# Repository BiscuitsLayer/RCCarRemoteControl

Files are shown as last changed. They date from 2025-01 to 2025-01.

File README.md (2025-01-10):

# План

## Все компоненты

1. Управлять с пульта (когда подаём команды с пульта, то машина сначала останавливается - то есть сбрасывается контроль с ПК)

2. Связь с камерой через удлинитель USB (с питанием) - если можно связь через провода, то лучше всегда её делать

## Настройка машинки

У тачки receiver RX-G3, есть 3 канала, у каждого канала есть по 3 пина

* Самый левый - сигнал (соединяется с белым проводом на машине при управлении только с пульта)
* Средний - питание +5V (соединяется с красным проводом на машине при управлении только с пульта)
* Самый правый - ground (соединяется с красным проводом на машине при управлении только с пульта)

Что-то типа такого ([источник](https://medium.com/@werneckpaiva/how-to-read-rc-receiver-signal-with-arduino-54e0447f6c3f)), только не 9 каналов, а 3, и питание и землю подаём для каждого отдельно

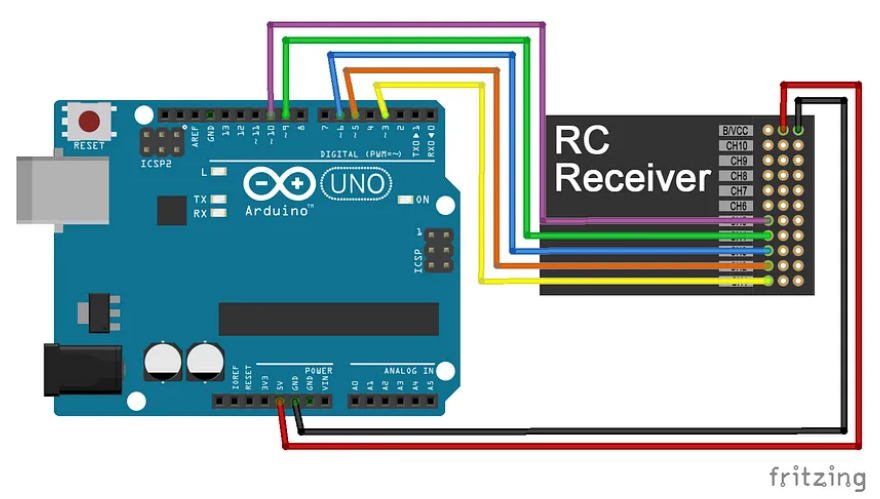
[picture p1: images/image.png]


<!-- Комментарий, потому что я использую Arduino Uno -->
<!-- Источник - это ШИМ (PWM), на Arduino Micro пины которые поддерживают ШИМ - 3, 5, 6, 9, 10, 11, 13 ([источник](https://forum.arduino.cc/t/pwm-from-pro-micro/618364/2)) -->

Далее описание самого левого пина на каждом из каналов

* На `CH1` - получатель с колёсика на пульте, поворот (steer)
* На `CH2` - получатель с курка на пульте, газ (speed)

<!-- Комментарий, потому что я использую Arduino Uno -->
<!-- Распиновка Arduino Micro (лучше ориентироваться по ней)
![alt text](images/image-1.png) -->

## Настройка Bluetooth на ПК (Windows)

[Видео с подключением модуля и базовым кодом на Python](https://www.youtube.com/watch?v=L3wjZOAyxEE) - это видео, в котором в целом описывается работа с модулем HC-05, который я использую. 

**Важно:** пароль по умолчанию - 1234

Чтобы Bluetooth на ПК увидел модуль на Windows, нужно выбрать `Bluetooth devices discovery -> Advanced`

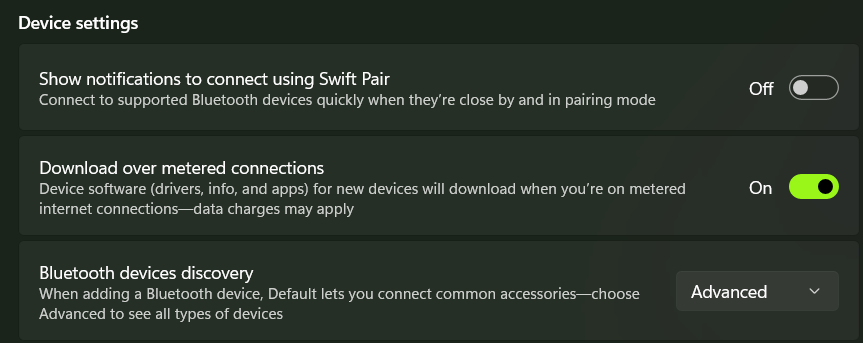
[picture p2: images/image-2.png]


Далее вниз где `Advanced Settings -> More Bluetooth settings -> COM Ports` и смотрим на `Outgoing` порт для HC-05

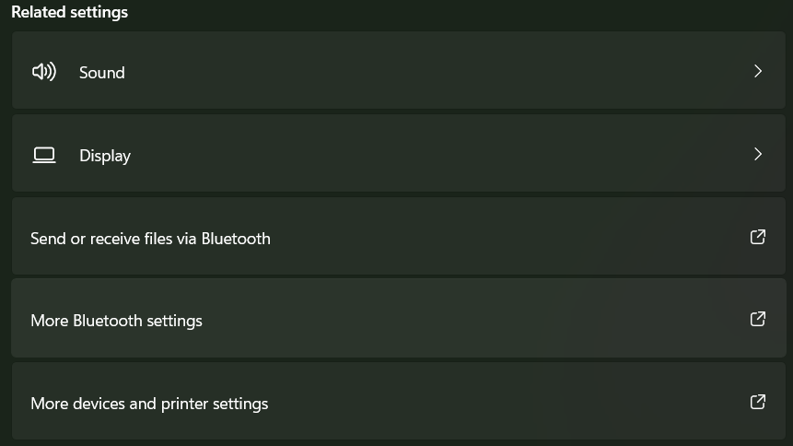
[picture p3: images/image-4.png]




У меня на компьютере используется порт `COM13`, поэтому в программе я использую его

**Очень важно:** иногда в окошке `COM Ports` значения портов пропадают - самый простой способ это починить (а я попробовал очень много способов) - перезагрузить компьютер

## Важные моменты, чтобы потом не забыть

1. Когда заливаем программу на Arduino Uno нужно вытащить провода из пинов 0 (RX) и 1 (TX), потому что они общаются по тому же каналу, что и вход на Arduino через USB. **Именно поэтому** если вставить Arduino в компьютер через USB и вытащить провода из 0 и 1 пинов, то можно общаться с Arduino через консоль в Arduino IDE так же, как это впоследствии нужно делать через Bluetooth

2. Каналы 0 (RX - receive) и 1 (TX - transmit) при вставленных провода нужно включать **соответственно** в TXD и RXD каналы Bluetooth модуля (чтобы то, что отправляет Arduino получал модуль Bluetooth и то что отправляет модуль Bluetooth получало Arduino)

3. Очень часто вылетают провода с землёй (GND) - она должна быть общей (соединена) у всех компонент, потому что иначе значения сигналов будут некорректными

4. PWM - широтно импульсная модуляция - какую-то часть периода держится сигнал HIGH, оставшуюся - сигнал LOW, таким образом передаются числовые значения. В среднем значение по каждому каналу (и steer и speed) примерно равно 1500. Не все пины на Arduino умеют работать с ШИМ - на Arduino UNO они помечены значком ~. Это порты 3, 5, 6, 9, 10, 11. Ещё у них разные частоты по умолчанию, которые можно менять ([подробнее](https://alexgyver.ru/lessons/pwm-overclock/)), но использование библиотеки Servo решает эту проблему

5. Для мотора (сервопривод с силой тяги 6 кг) основная частота 3000 Гц, это информация из интернета. Поэтому в коде для Arduino мы выставляем у servo максимальное значение в 3000. Для работы с сервоприводом через PWM используется библиотека Servo, которая по умолчанию уже есть в Arduino IDE - если попытаться вместо неё использовать `digitalWrite`, то работать не будет, потому что он умеет передавать только HIGH и LOW

6. Машинка устроена так, что двигатель должен постоянно питаться - иначе receiver не будет работать совсем

7. Arduino можно питать через `VIN` - пока это не используется и я питаю Arduino Uno от батарейки типа крона на 9 вольт

## Цвета и пины для проводов, чтобы потом не перепутать

Сначала разберёмся с Bluetooth модулем

* Питание 5V от Arduino UNO идёт в VCC на Bluetooth модуле (красный провод)
* GND от Arduino UNO идёт в GND на Bluetooth модуле (чёрный провод)
* 0 (RX) от Arduino UNO идёт в TXD на Bluetooth модуле (синий провод)
* 1 (TX) от Arduino UNO идёт в RXD на Bluetooth модуле (зелёный провод)

Далее нужно соединить ещё одну землю (GND) от Arduino UNO с землёй на Receiver-e - можно использовать любую, поэтому я использую GND от CH3, так как далее он пока всё равно не используется

У receiver-а они все уже соединены между собой - чтобы в этом убедиться их можно **прозвонить** - взять мультиметр, перевести его в режим прозвона - его обозначают динамиком или диодом. Проверить, что включили нужный режим, очень просто - для этого контакты щупов нужно соединить, и прибор издаст характерный звук, а на дисплее отображается нулевое или близкое к нулю значение. Итак, если земли GND соединены между собой, то поставив щупы на разные земли мы услышим характерный звук

Далее нужно соединить пины так, чтобы Arduino мог выступать в роли **прокси** - получать значения с одного пина и сразу же передавать их на другой

* Для поворота - будем получать их с сигнала CH1 receiver-a и передавать на 3 пин Arduino UNO (оранжевый провод, удвоенный) - поэтому в коде для ардуино `#define RC_CH1_INPUT 3`
* Для поворота - будем отдавать сигнал после обработки с 10 пина Arduino UNO на сигнал для поворота, который идёт в управление машинкой (зелёный провод, удвоенный) - поэтому в коде для ардуино `#define RC_CH1_OUTPUT 10`
* Для газа - будем получать их с сигнала CH2 receiver-a и передавать на 6 пин Arduino UNO (жёлтый провод, удвоенный) - поэтому в коде для ардуино `#define RC_CH2_INPUT 6`
* Для газа - будем отдавать сигнал после обработки с 9 пина Arduino UNO на сигнал для газа, который идёт в управление машинкой (синий провод, удвоенный) - поэтому в коде для ардуино `#define RC_CH2_OUTPUT 9`

Удвоенный провод == два провода соединены последовательно (один в другой), так проще программировать, но это совсем необязательно

Всё почти готово, осталось только передавать на питание и землю для поворота и газа (которые идут в управление машинкой) питание и землю с receiver-a. Для этого тоже используются красные провода (для питания) и чёрные провода (для земли)

## Немного про код для Arduino

Если собрать всё правильно и запустить, то можно управлять машинкой через `Serial Monitor` в Arduino IDE (нужно выбрать порт, с которым мы соединились по bluetooth - у меня это `COM13`)

Сами команды состоят из трёх чисел через запятую (без пробелов) - метки времени (при управлении вручную можно всегда делать равной 0), значения поворота и значения скорости. Какие бы значения мы не пытались передавать, они будут схлопнуты в нужный диапазон, поэтому можно смело передавать `0,0,0` и `0,2000,2000`. Чтобы всё остановилось нужно передать значения по умолчанию - `0,1500,1500` вполне подойдёт

Основная сложность в коде - обработка `intervention` - вмешательства с remote (пульта) когда мы пытаемся управлять с помощью bluetooth. В моём коде это реализовано так, что если поступил сигнал с пульта, который отличается от значения по умолчанию на `INTERVENTION_DELTA`, то управление по bluetooth отключается на `INTERVENTION_COOLDOWN_MILLIS` миллисекунд, и в это время можно управлять только с пульта. Если новых команд с пульта в течение `INTERVENTION_COOLDOWN_MILLIS` не поступило, мы снова начинаем принимать команды по bluetooth

Значение печатаются в консоль каждые `PRINT_COOLDOWN_MILLIS` миллисекунд. Отправка по bluetooth при вставленных проводах в 0 (RX) и 1 (TX) делается также как обычная печать в консоль при вставленном USB - с помощью `Serial.println`. Чтение по bluetooth  при вставленных проводах в 0 (RX) и 1 (TX) аналогично делается как чтение из консоли - с помощью `Serial.available()`, которая проверяет получены ли хоть какие-то данные и `Serial.readStringUntil('\n')` для чтения одной строки

Вроде бы я рассказал почти всё, если будет время то сделаю схему в Fritzing

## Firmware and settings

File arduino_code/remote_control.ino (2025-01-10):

#include <Servo.h>

#define SERIAL_PORT_SPEED 9600

#define PRINT_COOLDOWN_MILLIS 1000
bool need_to_write_intervention_detected_message = false;
bool need_to_write_car_is_controlled_by_remote_message = false;

#define INTERVENTION_DELTA 100
#define INTERVENTION_COOLDOWN_MILLIS 10000

#define RC_CH1_INPUT 3 // steer
#define RC_CH1_OUTPUT 10 // steer

#define RC_CH2_INPUT 6 // speed
#define RC_CH2_OUTPUT 9 // speed

unsigned long cur_time = 0;
unsigned long last_print_time = 0;
unsigned long last_intervention_time = 0;

Servo servo_channel_1; // steer
Servo servo_channel_2; // speed

#define AVG_CH1 1555
#define MIN_CH1 1179
#define MAX_CH1 1921 

#define AVG_CH2 1560
#define MIN_CH2 1070
#define MAX_CH2 1832

struct Command {
  unsigned long time;
  int steer;
  int speed;
};

// Function to check if there was a command from remote
bool remoteIntervention(int value, int avg_value) {
  // no signal from remote
  if (value == 0) {
    return false;
  }

  // if we received a strong value from remote, update last intervention time
  if (abs(value - avg_value) > INTERVENTION_DELTA) {
    need_to_write_intervention_detected_message = true;
    last_intervention_time = cur_time;
    return true;
  }

  // if intervention cooldown is still active but weak,
  // count it as an intervention (so car can be controlled by remote)
  // but do not update last_intervention_time
  if (cur_time - last_intervention_time < INTERVENTION_COOLDOWN_MILLIS) {
    need_to_write_car_is_controlled_by_remote_message = true;
    return true;
  }

  return false;
}

// Function to parse a command string into a Command structure
bool parseCommand(const String& commandString, struct Command& cmd) {
  int firstComma = commandString.indexOf(',');
  int secondComma = commandString.indexOf(',', firstComma + 1);

  if (firstComma == -1 || secondComma == -1) {
    // Invalid format, return false
    return false;
  }

  // Extract and convert each part of the command
  cmd.time = commandString.substring(0, firstComma).toInt();
  cmd.steer = commandString.substring(firstComma + 1, secondComma).toInt();
  cmd.speed = commandString.substring(secondComma + 1).toInt();

  return true;
}

void setup() {
  // Назначить пины D9 и D10 на 244 Гц 10bit
  // https://alexgyver.ru/lessons/pwm-overclock/
  // TCCR1A = 0b00000011;  // 10bit
  // TCCR1B = 0b00001011;  // x64 fast pwm

  // the default setting on HC-05 is typically at 9600 baud/second
  Serial.begin(SERIAL_PORT_SPEED); //ensure serial monitor is also set to 9600 baud

  pinMode(RC_CH1_INPUT, INPUT);
  servo_channel_1.attach(RC_CH1_OUTPUT, 0, 3000);

  pinMode(RC_CH2_INPUT, INPUT);
  servo_channel_2.attach(RC_CH2_OUTPUT, 0, 3000);

  cur_time = millis();
}

void loop() {
  cur_time = millis();

  // Handle control from remote (if intervention happened)
  int remote_channel_1_value = pulseIn(RC_CH1_INPUT, HIGH);
  if (remoteIntervention(remote_channel_1_value, AVG_CH1)) {
    servo_channel_1.writeMicroseconds(
      constrain(remote_channel_1_value, MIN_CH1, MAX_CH1)
    );
  }
  int remote_channel_2_value = pulseIn(RC_CH2_INPUT, HIGH);
  if (remoteIntervention(remote_channel_2_value, AVG_CH2)) {
    servo_channel_2.writeMicroseconds(
      constrain(remote_channel_2_value, MIN_CH2, MAX_CH2)
    );
  }

  // Handle control from console (or received from bluetooth)
  if (Serial.available() > 0) {
    String commandString = Serial.readStringUntil('\n');
    unsigned long millis_since_last_intervention = cur_time - last_intervention_time;

    // Ignore command if still under cooldown, otherwise apply
    if (millis_since_last_intervention < INTERVENTION_COOLDOWN_MILLIS) {
      Serial.println(
        "Command ignored because intervention happened recently\nIt happened " + 
        String(millis_since_last_intervention) + " millis ago and cooldown is " + 
        String(INTERVENTION_COOLDOWN_MILLIS)
      );
    } else {
      Command newCommand;

      if (parseCommand(commandString, newCommand)) {
        Serial.println("newCommand channel1 value: " + String(newCommand.steer));
        servo_channel_1.writeMicroseconds(
          constrain(newCommand.steer, MIN_CH1, MAX_CH1)
        );

        Serial.println("newCommand channel2 value: " + String(newCommand.speed));
        servo_channel_2.writeMicroseconds(
          constrain(newCommand.speed, MIN_CH2, MAX_CH2)
        );
      } else {
        Serial.println("Failed to parse command");
      }
    }
  }

  // Output current PWM values to console (or send via bluetooth)
  if (cur_time - last_print_time > PRINT_COOLDOWN_MILLIS) {
    Serial.println("Channel1 value: " + String(servo_channel_1.readMicroseconds()));
    Serial.println("Channel2 value: " + String(servo_channel_2.readMicroseconds()));

    if (need_to_write_car_is_controlled_by_remote_message) {
      Serial.println("Car can be controlled by remote now");
      need_to_write_car_is_controlled_by_remote_message = false;
    }
    if (need_to_write_intervention_detected_message) {
      Serial.println("New intervention from remote detected");
      need_to_write_intervention_detected_message = false;
    }
    Serial.println();

    last_print_time = cur_time;
  }
}

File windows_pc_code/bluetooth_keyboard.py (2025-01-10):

import sys
import time
import serial
from pynput import keyboard

# Configure the serial connection
# TODO: also can choose port automatically (by searching the name of paired device) 
# COM13 выбран сейчас для взаимодействия с Arduino HC-05, подробнее 
# можно посмотреть в настройках bluetooth в Windows нажав "Подробнее"
ser = serial.Serial('COM13', baudrate=9600, timeout=1)

# Эти значения взяты из файла для Arduino
# channel 1 == steer
# channel 2 == speed
AVG_CH1 = 1555
MIN_CH1 = 1179
MAX_CH1 = 1921 

AVG_CH2 = 1560
MIN_CH2 = 1070
MAX_CH2 = 1832

cur_steer = AVG_CH1
cur_speed = AVG_CH2

def write_command(time_stamp, steer, speed):
    # Format the command as "time,steer,speed\n"
    command = f"{time_stamp},{steer},{speed}\n"
    ser.write(command.encode())  # Write the command as bytes
    print(f"Sent: {command.strip()}")  # For debugging

# Обработчики для каждой клавиши
def handle_w_pressed():
    global cur_speed
    cur_speed = AVG_CH2 + 200
    current_time = int(time.time() * 1000)
    write_command(current_time, cur_steer, cur_speed)
    print("W нажата")

def handle_s_pressed():
    global cur_speed
    cur_speed = AVG_CH2 - 400
    current_time = int(time.time() * 1000)
    write_command(current_time, cur_steer, cur_speed)
    print("S нажата")

def handle_a_pressed():
    global cur_steer
    cur_steer = AVG_CH1 + 200
    current_time = int(time.time() * 1000)
    write_command(current_time, cur_steer, cur_speed)
    print("A нажата")

def handle_d_pressed():
    global cur_steer
    cur_steer = AVG_CH1 - 200
    current_time = int(time.time() * 1000)
    write_command(current_time, cur_steer, cur_speed)
    print("D нажата")

def handle_w_released():
    global cur_speed
    cur_speed = AVG_CH2
    current_time = int(time.time() * 1000)
    write_command(current_time, cur_steer, cur_speed)
    print("W отпущена")

def handle_s_released():
    global cur_speed
    cur_speed = AVG_CH2
    current_time = int(time.time() * 1000)
    write_command(current_time, cur_steer, cur_speed)
    print("S отпущена")

def handle_a_released():
    global cur_steer
    cur_steer = AVG_CH1
    current_time = int(time.time() * 1000)
    write_command(current_time, cur_steer, cur_speed)
    print("A отпущена")

def handle_d_released():
    global cur_steer
    cur_steer = AVG_CH1
    current_time = int(time.time() * 1000)
    write_command(current_time, cur_steer, cur_speed)
    print("D отпущена")

# Словарь для хранения состояний клавиш
keys_pressed = {
    'w': False,
    'a': False,
    's': False,
    'd': False
}

def on_press(key):
    try:
        if key.char == 'w' and not keys_pressed['w']:
            keys_pressed['w'] = True
            handle_w_pressed()
        elif key.char == 'a' and not keys_pressed['a']:
            keys_pressed['a'] = True
            handle_a_pressed()
        elif key.char == 's' and not keys_pressed['s']:
            keys_pressed['s'] = True
            handle_s_pressed()
        elif key.char == 'd' and not keys_pressed['d']:
            keys_pressed['d'] = True
            handle_d_pressed()
        elif key.char == 'q':
            print("\nПрограмма завершена.")
            sys.exit(0)  # Выход из программы
    except AttributeError:
        pass

def on_release(key):
    try:
        if key.char == 'w' and keys_pressed['w']:
            keys_pressed['w'] = False
            handle_w_released()
        elif key.char == 'a' and keys_pressed['a']:
            keys_pressed['a'] = False
            handle_a_released()
        elif key.char == 's' and keys_pressed['s']:
            keys_pressed['s'] = False
            handle_s_released()
        elif key.char == 'd' and keys_pressed['d']:
            keys_pressed['d'] = False
            handle_d_released()
    except AttributeError:
        pass

def main():
    with keyboard.Listener(on_press=on_press, on_release=on_release) as listener:
        listener.join()

if __name__ == "__main__":
    main()
